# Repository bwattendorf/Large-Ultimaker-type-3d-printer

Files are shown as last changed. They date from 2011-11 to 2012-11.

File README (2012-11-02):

Ultimaker-Electronics
=====================

Large Ultimaker box design  

Designed by Ultimaker origional modified by Bruce Wattendorf

licensed under the Attribution - Share Alike - Creative Commons license.

http://creativecommons.org/licenses/by-sa/3.0/

I have cut this and found that the Z axis needs 3 steppers which can be driven by the same stepper driver.

Also the build platform needs 2 more solid rods in the front. 

Changes to be done

move the electronics to the back the cable gets in the way

add lcd and encoder 

add 1 more z axis stepper in the front

make slot for the sd card in the side close to the electronics 

reinforce the build platform solid rods mount and make the floating one fixed like the right side

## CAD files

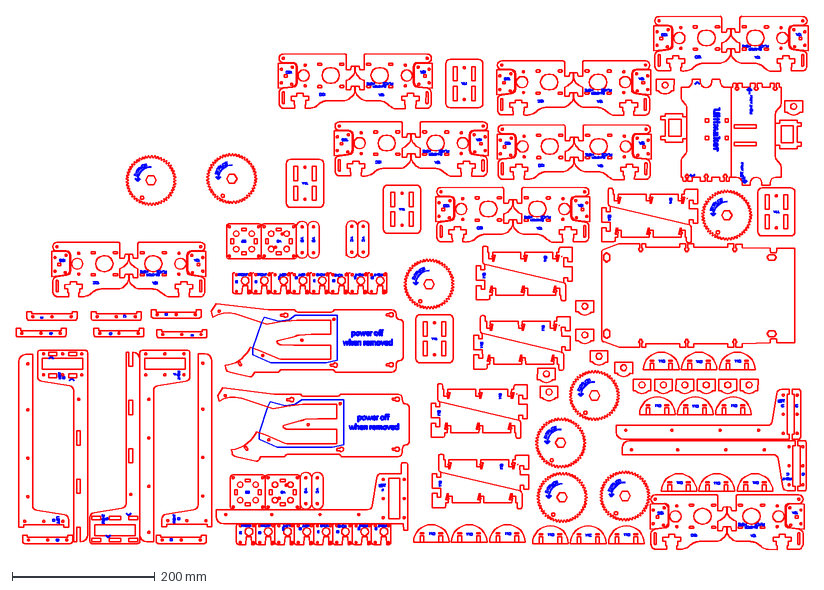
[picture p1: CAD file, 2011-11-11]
new cut sheets/make it labs 4 x 3/origional cut sheets/all cut sheets we need/6mm plywood full parts sheet 8.dxf
1108.4 x 746.0 mm

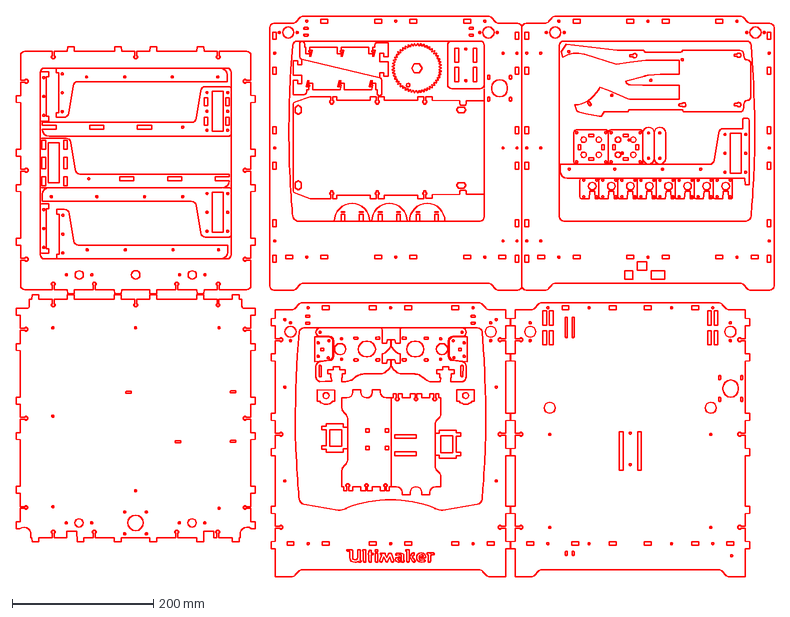
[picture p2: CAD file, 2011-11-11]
new cut sheets/make it labs 4 x 3/origional cut sheets/small ultimaker full sheet files/Ultimaker full all parts.dxf
1073.5 x 793.8 mm

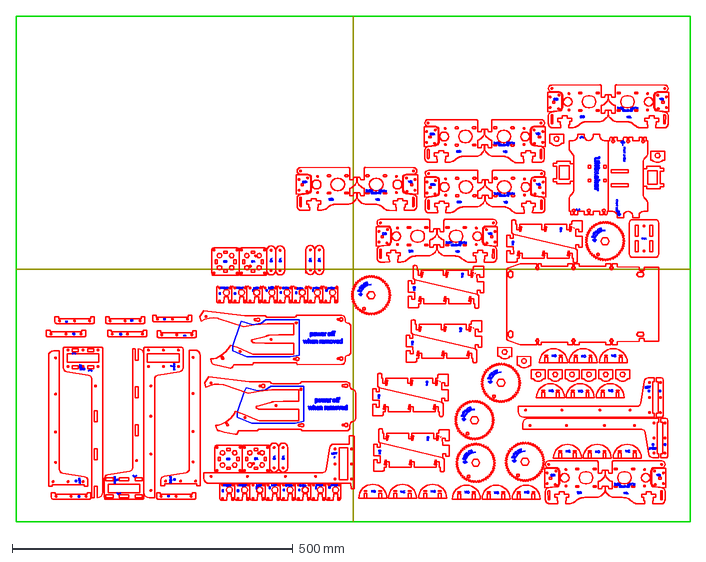
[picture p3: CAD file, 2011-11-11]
new cut sheets/make it labs 4 x 3/6mm plywood full parts sheet.dxf
1200.0 x 900.0 mm

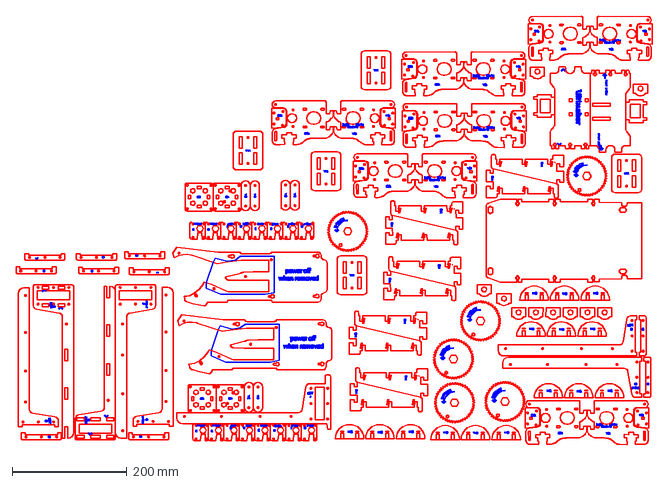
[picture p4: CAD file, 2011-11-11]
new cut sheets/make it labs 4 x 3/origional cut sheets/6mm plywood full parts sheet 8.dxf
1108.4 x 746.0 mm

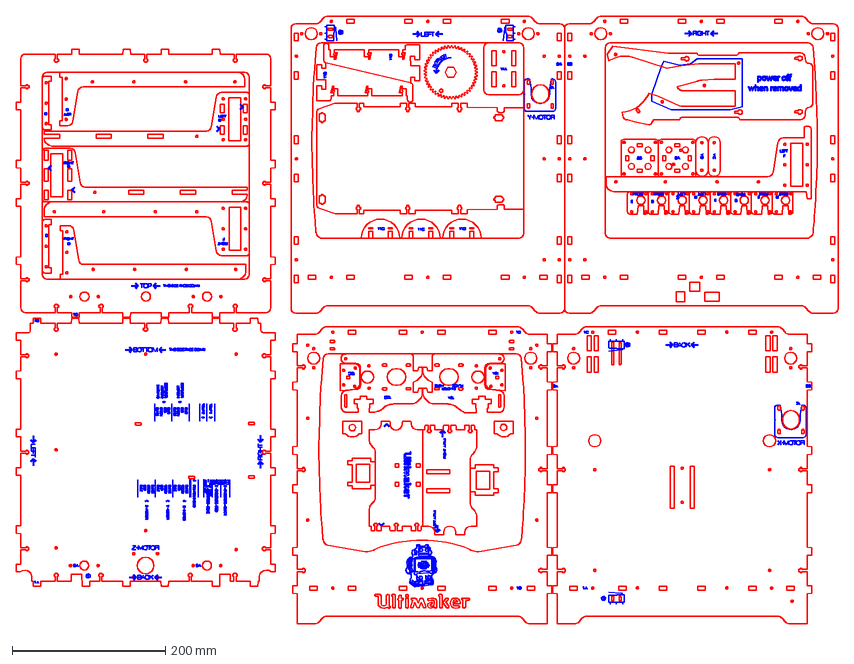
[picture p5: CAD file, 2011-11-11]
new cut sheets/make it labs 4 x 3/origional cut sheets/all cut sheets we need/Ultimaker full all parts.dxf
1073.5 x 793.8 mm

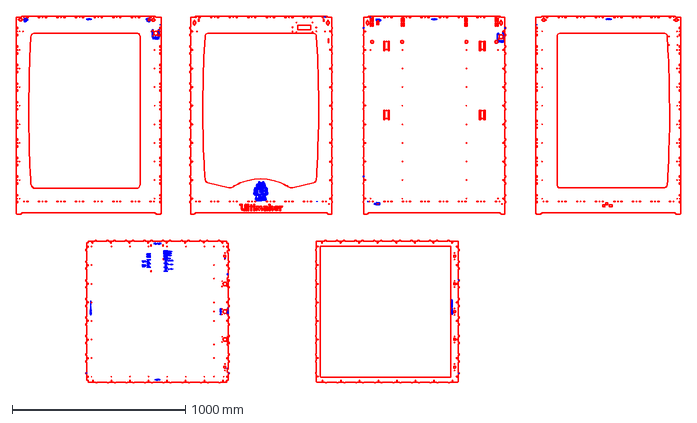
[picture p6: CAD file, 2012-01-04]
larger sized ultimaker files/new 5.2 mm large case.DXF
3838.0 x 2118.2 mm

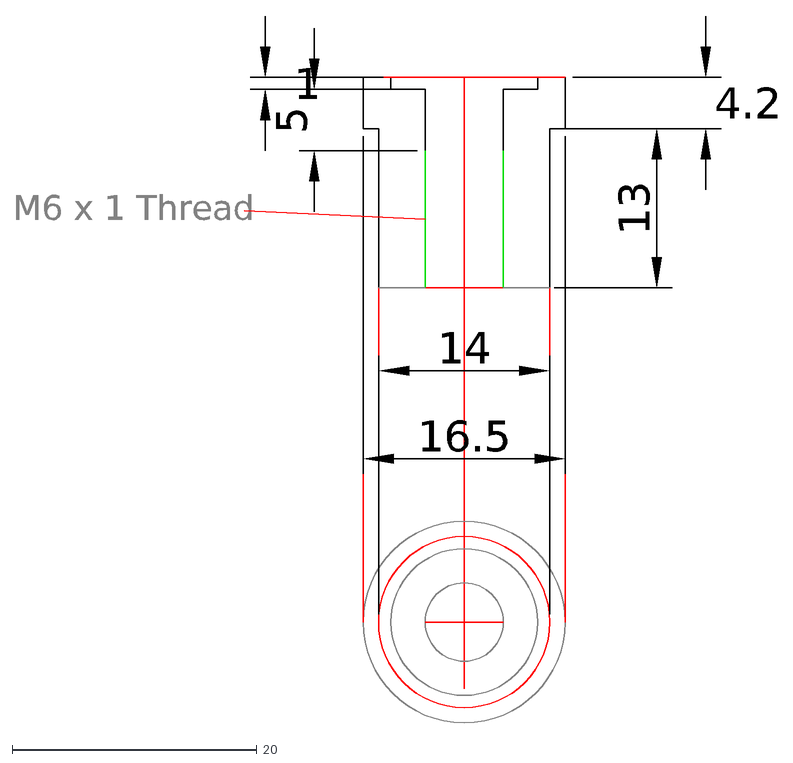
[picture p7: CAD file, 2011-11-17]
machined parts drawings/peek insulator.dxf
1
5
4.2
13
16.5
14
M6 x 1 Thread

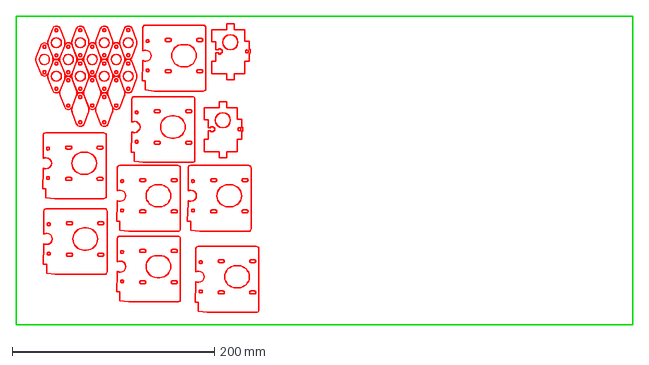
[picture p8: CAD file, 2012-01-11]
new cut sheets/as220 laser 1 x 2/1-8 ply sheet 2 cuts.dxf
609.6 x 304.8 mm

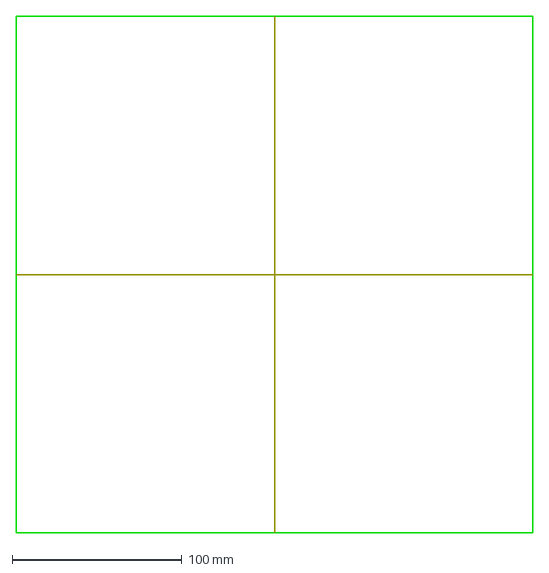
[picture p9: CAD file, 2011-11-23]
new cut sheets/laser cutter table templats/as220 1 x 1.dxf
304.8 x 304.8 mm

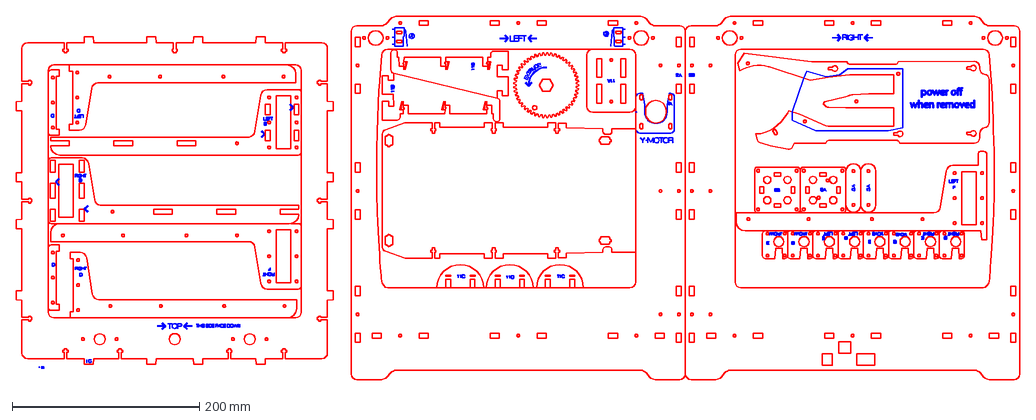
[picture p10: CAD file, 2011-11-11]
new cut sheets/make it labs 2 x 4/2 x4 small with parts/small with parts sheet1 .dxf
1071.9 x 388.0 mm

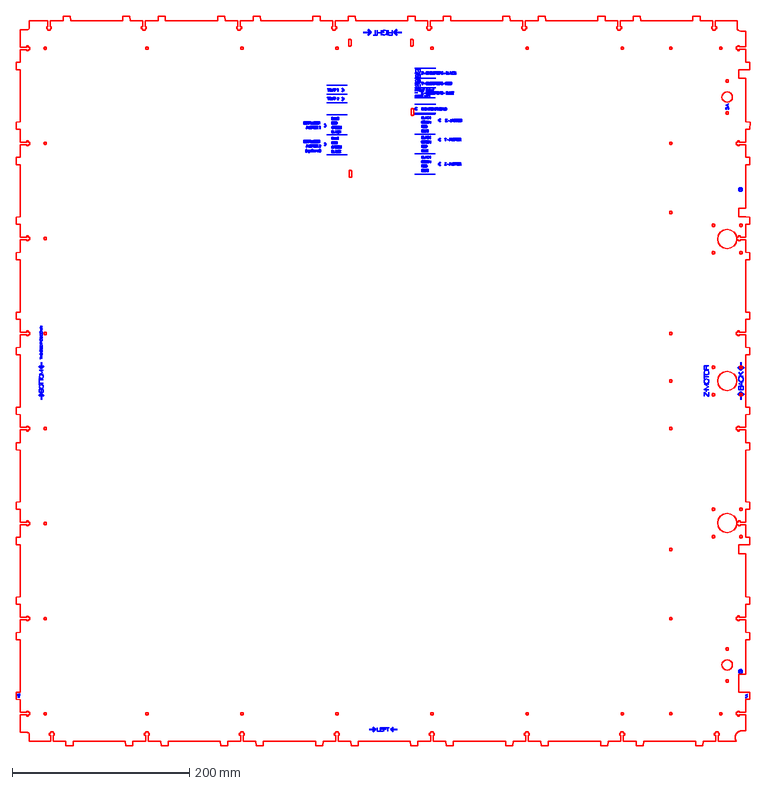
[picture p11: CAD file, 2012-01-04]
new cut sheets/make it labs 4 x 3/new 5mm bottom.dxf
828.6 x 823.1 mm

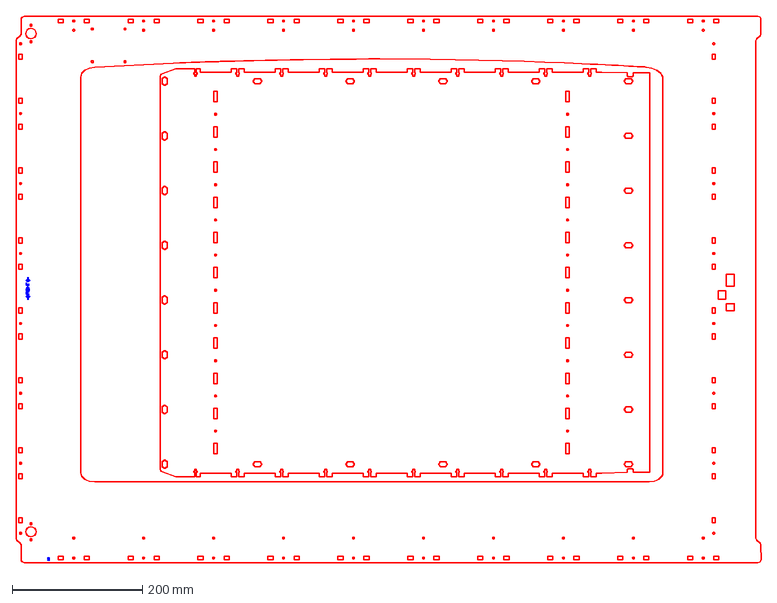
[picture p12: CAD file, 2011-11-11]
new cut sheets/make it labs 4 x 3/origional cut sheets/6mm plywood sheet 2 rightside.dxf
1143.0 x 838.0 mm

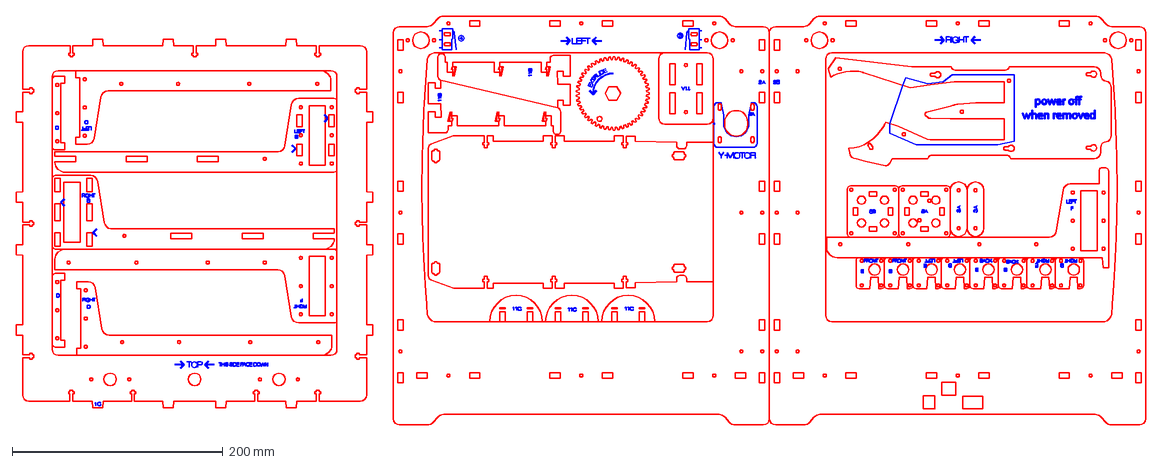
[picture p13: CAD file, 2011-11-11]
new cut sheets/make it labs 4 x 3/origional cut sheets/all cut sheets we need/small with parts sheet1 .dxf
1071.9 x 388.0 mm

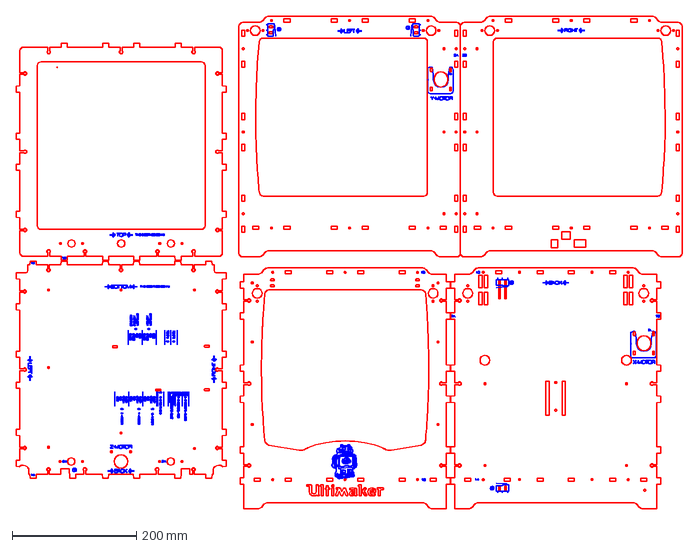
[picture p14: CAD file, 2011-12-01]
new cut sheets/make it labs 4 x 3/origional cut sheets/small ultimaker full sheet files/Ultimaker just case.dxf
1073.5 x 793.8 mm

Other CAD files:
normal sized ultimaker files/ultimaker.dxf
larger sized ultimaker files/new 5.2mm build platform sheet.DXF
new cut sheets/as220 laser 1 x 2/1-8 ply sheet 2 text.dxf
new cut sheets/laser cutter table templats/1 8 inch derlin.dxf
machined parts drawings/aluminum extruder heat plate.dxf
machined parts drawings/extruder heater block .dxf
machined parts drawings/x y slide bushing.dxf
machined parts drawings/z axis acme threaded rod nut.dxf
new cut sheets/as220 laser 1 x 2/1 4 sheet15.dxf
new cut sheets/as220 laser 1 x 2/1 8 sheet16.dxf
new cut sheets/as220 laser 1 x 2/1-4 del sheet 7 cuts.dxf
new cut sheets/as220 laser 1 x 2/1-4 ply sheet 1 cuts.dxf
new cut sheets/as220 laser 1 x 2/1-4 ply sheet 1 text.dxf
new cut sheets/as220 laser 1 x 2/1-4 ply sheet 1.dxf
new cut sheets/as220 laser 1 x 2/1-4 ply sheet1 cuts.dxf
new cut sheets/as220 laser 1 x 2/1-4 ply sheet1 text.dxf
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

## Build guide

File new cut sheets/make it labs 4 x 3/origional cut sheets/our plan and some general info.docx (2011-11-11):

Goals in order

1. Make the large Ultimaker frame and large parts
2. Make 2 small Ultimaker frames
3. Make a small Ultimaker for make it labs with ¼ “ parts
4. Make the parts for our 3 Ultimakers

Plywood size

Make it labs laser table size is 1200 x 900 mm (47.2 x 35.4 inches)

List of sheets we need to cut in order.

1. 6mm plywood sheet 1 backside.dxf
2. 6mm plywood sheet 2 rightside.dxf
3. 6mm plywood sheet 3 leftside.dxf
4. 6mm plywood sheet 4 frontside.dxf
5. 6mm plywood sheet 5 topside.dxf
6. 6mm plywood sheet 6 bottomside.dxf
7. 4mm_birch sheet7 parts.dxf
8. Small ultimaker shell sheet 1.dxf
9. Small ultimaker shell sheet2.dxf
10. Small with parts sheet1 . dxf
11. Small with parts sheet2.dxf
12. Ultimaker full all parts.dxf
13. 6mm plywood full parts sheet 8.dxf

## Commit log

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2011-10-24 this is the initial add of my current files before i have scaled them up
    [3mm delrin sheet 10 extruder parts.dxf, 4mm_birch sheet7 parts.dxf, 6mm acrylic sheet 9 build platform with makerbot extruder.dxf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]
2011-10-24 added cut sheets for 2 x 4 6mm sheets for origional Ultimaker
    [4x8 6mm sheet1.dxf, 4x8 6mm sheet2.dxf]
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2011-10-26 I remade the origional file from thingiverse rev2 and then broke out all of the layers again I also split out the files by type for the origional sheets
    [UltimakerLasercutDrawings_0.5mm_polypropylene.dxf, UltimakerLasercutDrawings_3mm_delrin.dxf, UltimakerLasercutDrawings_4mm_birch.dxf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]
2011-10-26 changed the 5.2 mm birch file to narrow the slots for the board to go into
    [UltimakerLasercutDrawings_5_2mm_birch.dxf]
2011-10-27 cleaned up folders again planing on making one sheet have the changes so i can post it on thingiverse
    [UltimakerLasercutDrawings_0.5mm_polypropylene.dxf, UltimakerLasercutDrawings_3mm_delrin.dxf, UltimakerLasercutDrawings_4mm_birch.dxf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]
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2011-10-27 Added 2nd extruder and also made one 4mm platform arm on each side to the 5.2 mm so that it will be the same size as Ultimaker I hope this will not be an issue it looks like it should not be any prob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
    I still just need to add wire hold down holes to the inside back
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2011-10-28 added all the parts to the large back side and also moved over the working copy
    [6mm plywood sheet 1 backside.dxf]
2011-10-28 Finihsed off the large back panel and also added wire support holes to the normal sized machine
    [6mm plywood sheet 1 backside.dxf]
2011-10-31 fixed up the first 3 large sheet and found a issue on the normal sheet (something was selected as text now fixed)
    [6mm plywood sheet 2 rightside.dxf, 6mm plywood sheet3 leftside.dxf]
2011-10-31 removed some files not needed and started the large front sheet 4
    [6mm plywood sheet4 frontside old.dxf, 6mm plywood sheet4 frontside.dxf, 6mm plywood sheet4 frontsidewith thing o matic.dxf]
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2011-10-31 made a large 5.2 mm master sheet so i can make sure every thing is lined up and also make new top and bottom boards
    [new 5.2 mm large master sheet.DXF]
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2011-10-31 Lined up and sized the top large on the large master working copry still have to bring it back to the top sheet and fix the nut slots and holes
    [new 5.2 mm large master sheet.DXF]
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2011-10-31 fixed the back side the top holes were not adjusted to new dimention also added the new back to the large master so i can check the sheets before i fix the top and bottom again
    [6mm plywood sheet 1 backside.dxf]
2011-11-01 made new large sheet 5 and sheet 6 still need to clean them up
    [6mm plywood sheet5 topside.dxf, 6mm plywood sheet6 bottomside.dxf]
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2011-11-01 cleaned up and added the new screw holes on both top and bottom also added the stuff to the bottom except the support rod holes on both also need to make the center hole on the top larger and add the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
    [6mm plywood sheet5 topside.dxf, 6mm plywood sheet6 bottomside.dxf]
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2011-11-01 Finished off the Large top sheet 5 I need to make sure the support rod holes are lined up though
    [6mm plywood sheet5 topside.dxf]
2011-11-01 finished up the bottom board added new support rod holes
    I need to check and make sure they line up when done with build table
    [6mm plywood sheet6 bottomside.dxf]
2011-11-01 fixed text on the normal sized master sheet and also started the build platforma so i added a new master sheet
    [new 5.2mm build platform sheet.DXF]
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2011-11-02 i fixed the screw holes on the build platform stage on the large master
    [new 5.2mm build platform sheet.DXF]
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2011-11-02 Found I had to redue all of the build platform parts Yuck!! next time i will make sure to check the initial files to make sure they are scaled right first!
    [new 5.2mm build platform sheet.DXF]
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2011-11-02 fixed the build platform some more and also finished off the top and bottom sheet I added the rod holes in the right place
    [6mm plywood sheet5 topside.dxf, 6mm plywood sheet6 bottomside.dxf, new 5.2mm build platform sheet.DXF]
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2011-11-03 worked on the build platform and added new files for laser cutted templates
    [as220 1 x 2.dxf, make it labs 4 x 2.dxf, make it labs 4 x 3.dxf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]
2011-11-03 resized the build platform base teeth so they will fit better with 5.2 mm plywood
    [new 5.2mm build platform sheet.DXF]
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2011-11-03 added referance lines to the laser sheets and readded the top and bottom to the large master sheet
    [as220 1 x 2.dxf, make it labs 4 x 2.dxf, make it labs 4 x 3.dxf]
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2011-11-04 i got all of the sheets done now just looking thru to make sure every thing is good to push the button also added the 4mm birch large new sheet
    [4mm_birch sheet7 parts.dxf, Ultimaker full all parts.dxf, Ultimaker just case.dxf]
2011-11-04 cleaned up some more a little removed some of the referance lines
    [6mm plywood sheet5 topside.dxf, Ultimaker full all parts.dxf, small ultimaker shell sheet 1.dxf]
2011-11-04 Added AS220 laser cutter sheets i still need to add derlin and acrylic sheets
    [4 mm sheet10 parts.dxf, 4 mm sheet11 parts.dxf, 5.2 mm sheet master.dxf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]
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2011-11-08 changed the front logo to be a cut thru not a engrave like the logo image
    [6mm plywood sheet4 frontside.dxf, Ultimaker full all parts.dxf, Ultimaker just case.dxf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]
2011-11-10 did a little bit of work on the files before we cut
    [1 4 inch derlin.dxf, 1 8 inch derlin.dxf, 4 mm sheet10 parts.dxf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]
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2011-11-11 Added all of the parts to the parts sheet but have not finished yet
    [6mm plywood full parts sheet.dxf]
2011-11-11 added a bunch made some new sheets and made a folder with all of the files we need for sunday
    [4mm_birch sheet7 parts.dxf, 6mm plywood full parts sheet 8.dxf, 6mm plywood sheet 1 backside.dxf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]
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2011-11-11 cleaned up the files a little but more getting ready to laser cut
    [4mm_birch sheet7 parts.dxf, 6mm plywood sheet 1 backside.dxf, 6mm plywood sheet3 leftside.dxf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]
2011-11-11 cleaned up a bunch more removed a lot of extra lines and reziped the folder of files
    [6mm plywood sheet 1 backside.dxf, 6mm plywood sheet 2 rightside.dxf, 6mm plywood sheet3 leftside.dxf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]
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2011-11-17 added a bunch of .dxf drawings of the parts that need to be machined and the electronic scmatics
    [Arduino_MEGA_Ultimaker_Shield_v1.5.4.brd, Arduino_MEGA_Ultimaker_Shield_v1.5.4.sch, aluminum extruder heat plate.dxf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]
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2011-11-21 made some more changes to the files and removed all of the as220 cust so i can remoke them again
    [4 mm sheet10 parts.dxf, 4 mm sheet11 parts.dxf, 5.2 mm sheet master.dxf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]
2011-11-22 made some more changes and added all of my 5.2 as220 sheets now i need to clean them up
    [5.2 sheet5.dxf, 5.2 sheet6.dxf, 5.2 sheet7.dxf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]
2011-11-22 cleaned up the 5.2 mm master sheets before i post them on thingiverse still need to fix the tabs
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2011-12-29 fixed top and bottom and double checked the tabs and alighnment
    [new 5.2 mm large case.DXF, new top and bottom.dxf]
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
